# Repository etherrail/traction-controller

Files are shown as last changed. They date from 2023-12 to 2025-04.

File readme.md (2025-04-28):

# EtherRail Traction Controller TC1000PX22+D+EA
The WiFi based controller for locomotives and other rolling stock.
This device is a drop in replacement for any DCC boards.

Main Features
- WiFi enabled
- Plux2 Interface according to [NEM 658](./documentation/nem658.pdf)
- Inertia Sensor for speed control (instead of the common power control)
- Sound up to 96kHz
- 1A motor current (3.6A Peak)
- Track power probe
- Low production cost
- Tip over, stall and push detection

Product Code
- `TC` traction controller
- `1000` 1000mA nominal current
- `PX22` PluX22 plugging interface (NEM 658)
- `+D` debugging version (USB compatible, status LEDs)
- `+CA` external antenna

## To Do
- Test Boards (currently in production)
- Add GPIO pins

## Connectivity
The device connects with WiFi or Bluetooth.
An external antenna should be attached.

## Ineria Sensor
Usually, the trains are controlled by setting a motor power level, not a target speed. The IMU sensor integrates an accelerometer and a gyroscope, which can be used to estimate the actual speed of the train.

No more speed calibrations and motor ramps - the controller can automatically compensate for heavier trains or gradients. Stalling can be detect too, both total stalling and wheel-slip, which can then be counter acted with automatically induced power bursts. The controller can detect being pushed too, for example in a collision case. And even a tip over can be detected.

## Track Power Probe
The traction controller constantly measures the track voltage.
When an outage is detected (which usually happens every couple miliseconds, even with clean tracks), the controller goes into sleep mode to preserve energy on the on board capacitor bank.

This can be used to monitor the tracks quality and schedule maintenance before issues arise.

## Sound
The board contains a 3.2W@4Ohm sound chip.

To be tested.

## Function Outputs
600mA per channel.

Warning: The output are directly connected to the P-Channel mosfets, additional protected may be required for some output devices.

## Expandability
The processor used on this device (ESP32C3) is more than capable for this task.
We could add camera functionality with this chip!
DCC emulation is theoretically possible.

The board currently contains a full USB debugging interface (pads only, but a programmer is included on the ESP).

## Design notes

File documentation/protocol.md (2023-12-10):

# Traction Controller Client Protocol (TCCP)
This document describes the TCP-socket based protocol used to interface with etherrail traction controllers. This protocol may be used by any other Wifi-based traction controller, but modifications should be posed as issues on here to create a common standard.

The traction controller does not store **any** settings. Every setting has to be reapplied on startup.

## Sent by traction controller
Listed are the packages sent by the traction controller.
A orchestrator has to handle all the messages sent by traction controllers.

### `0x00` Keep Alive
The traction controller will send this package every **250ms**. The traction controller should be flagged as dead when no package (not just keep alive) was received for over **1000ms**.

### `0x21 [Quality]` Power Quality
The traction controller may periodically send this package to report the current track quality. We are sending it every 25mm in testing, but this may be decreased and only reported when the quality is poor. 

The quality parameter ranges from 0 (0V track voltage) to 255 (20V track voltage).

## Sent by orchestrator
The orchestrator sends commands to the traction controller. All commands are listed here.

### `0x00` Keep Alive
This package should be sent every **250ms**. The orchestrator has to send any package every **1000ms** or the traction controller will automatically perform an emergency stop. 

### `0x01` Emergency Stop
The traction controller will perform and emergency stop.

### `0x91 [Speed]` Set Speed
The traction controller will apply the speed as a voltage to the motor. 

Speed 0 will stop the motor, while 255 will apply the maximum voltage set by [Maximum Motor Voltage](#0xa1-max-voltage-maximum-motor-voltage).

### `0xa1 [Max Voltage]` Maximum Motor Voltage
This setting prevents motor damage. Any speed operations will automatically be scaled by the maximum voltage. Max voltage parameter ranges from 0 = 0V to 255 = 20V. 

Example: `0xa1 0x7f 0x91 0xff` will apply 10V to the motor, while a following `0x91 0x7f` will apply 5V.

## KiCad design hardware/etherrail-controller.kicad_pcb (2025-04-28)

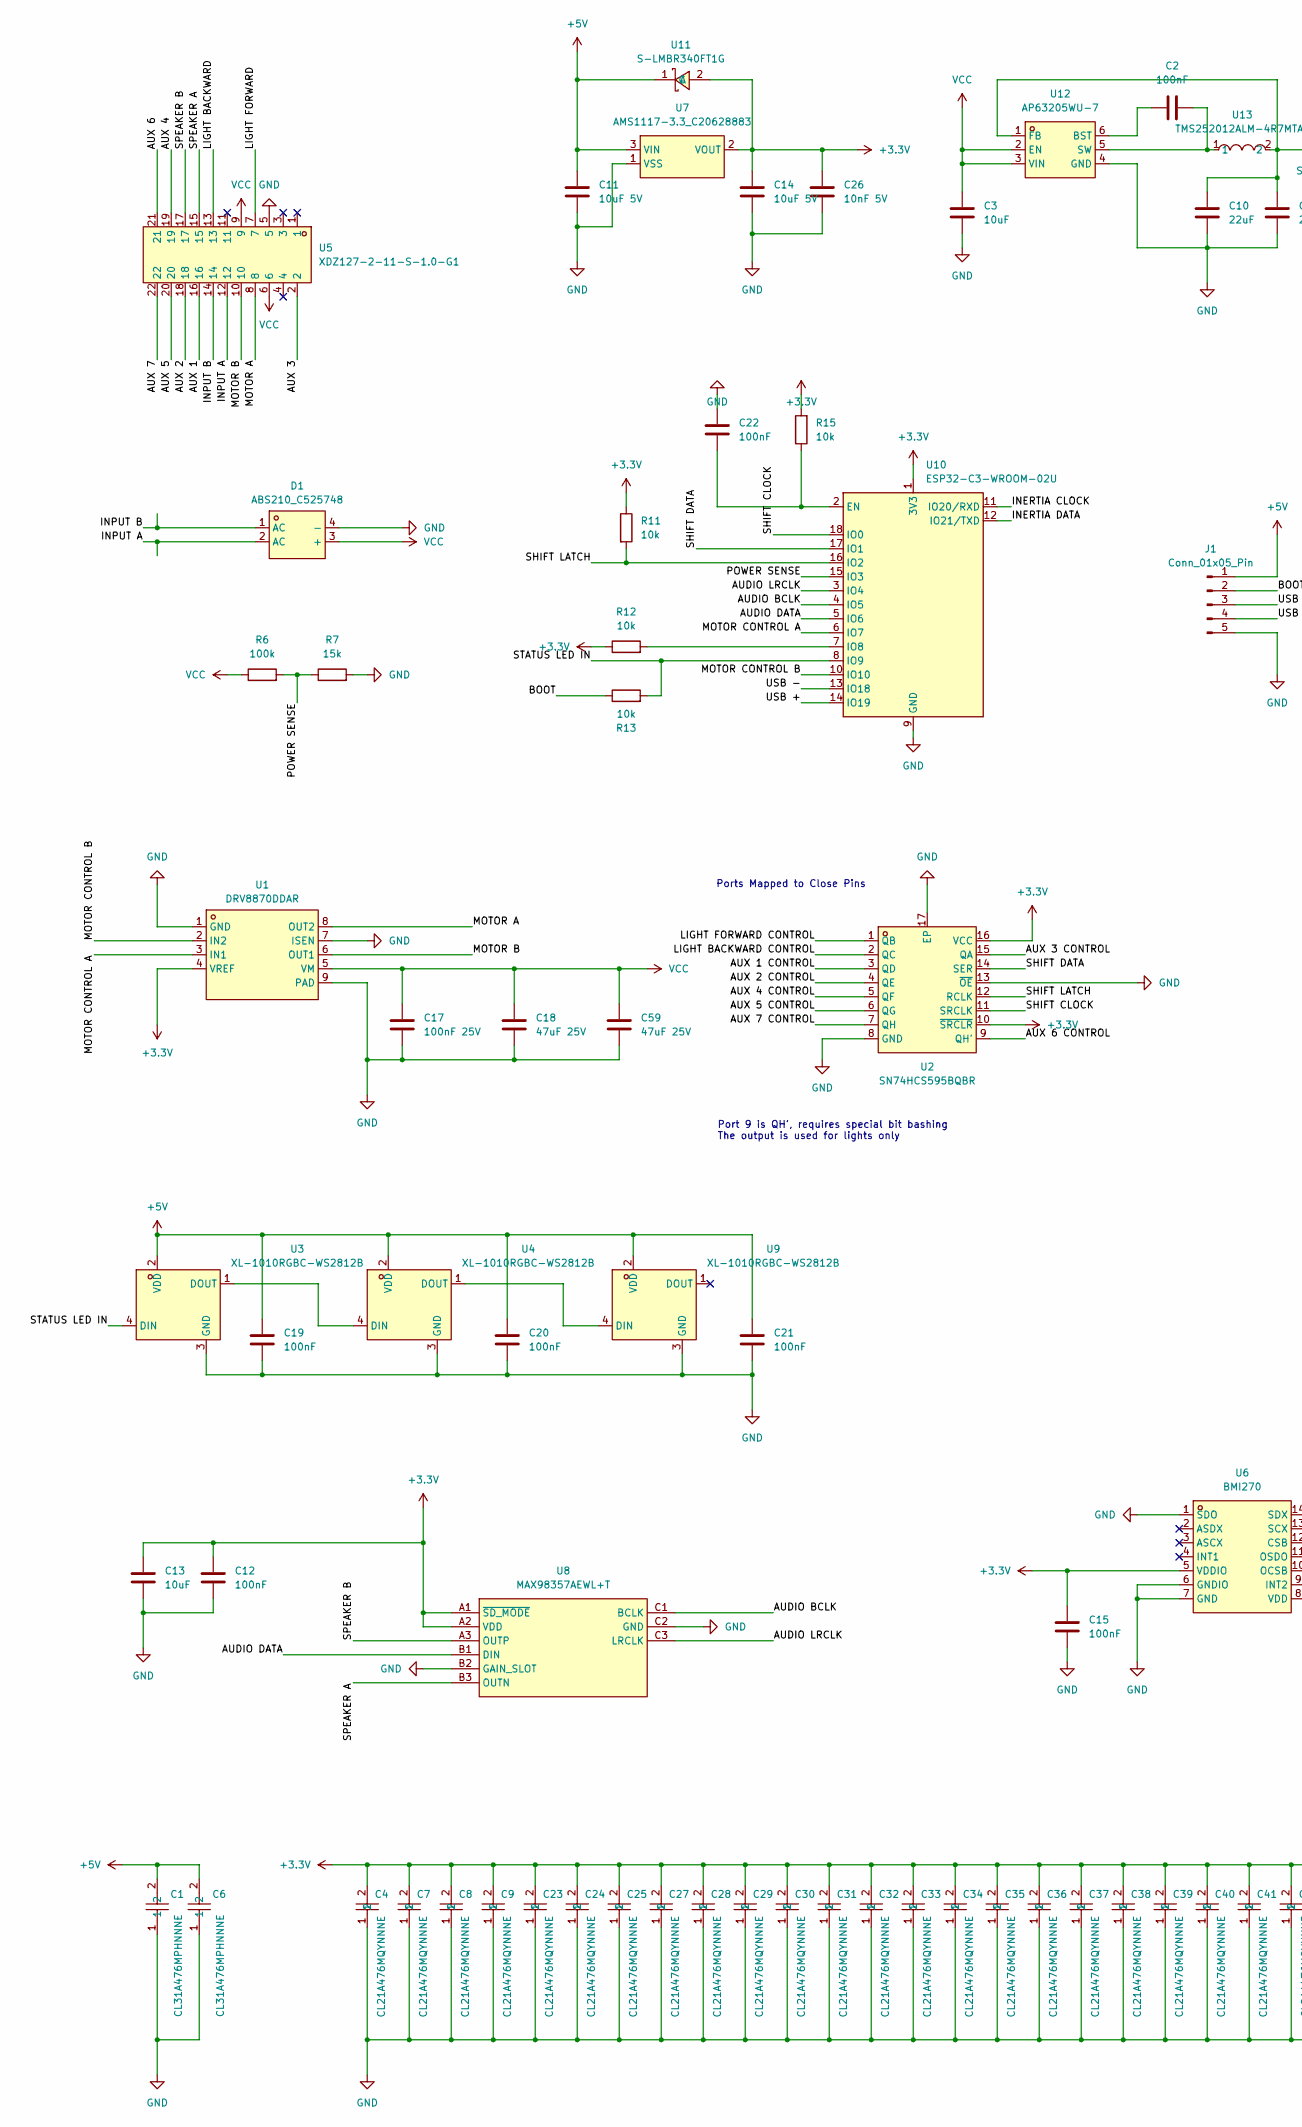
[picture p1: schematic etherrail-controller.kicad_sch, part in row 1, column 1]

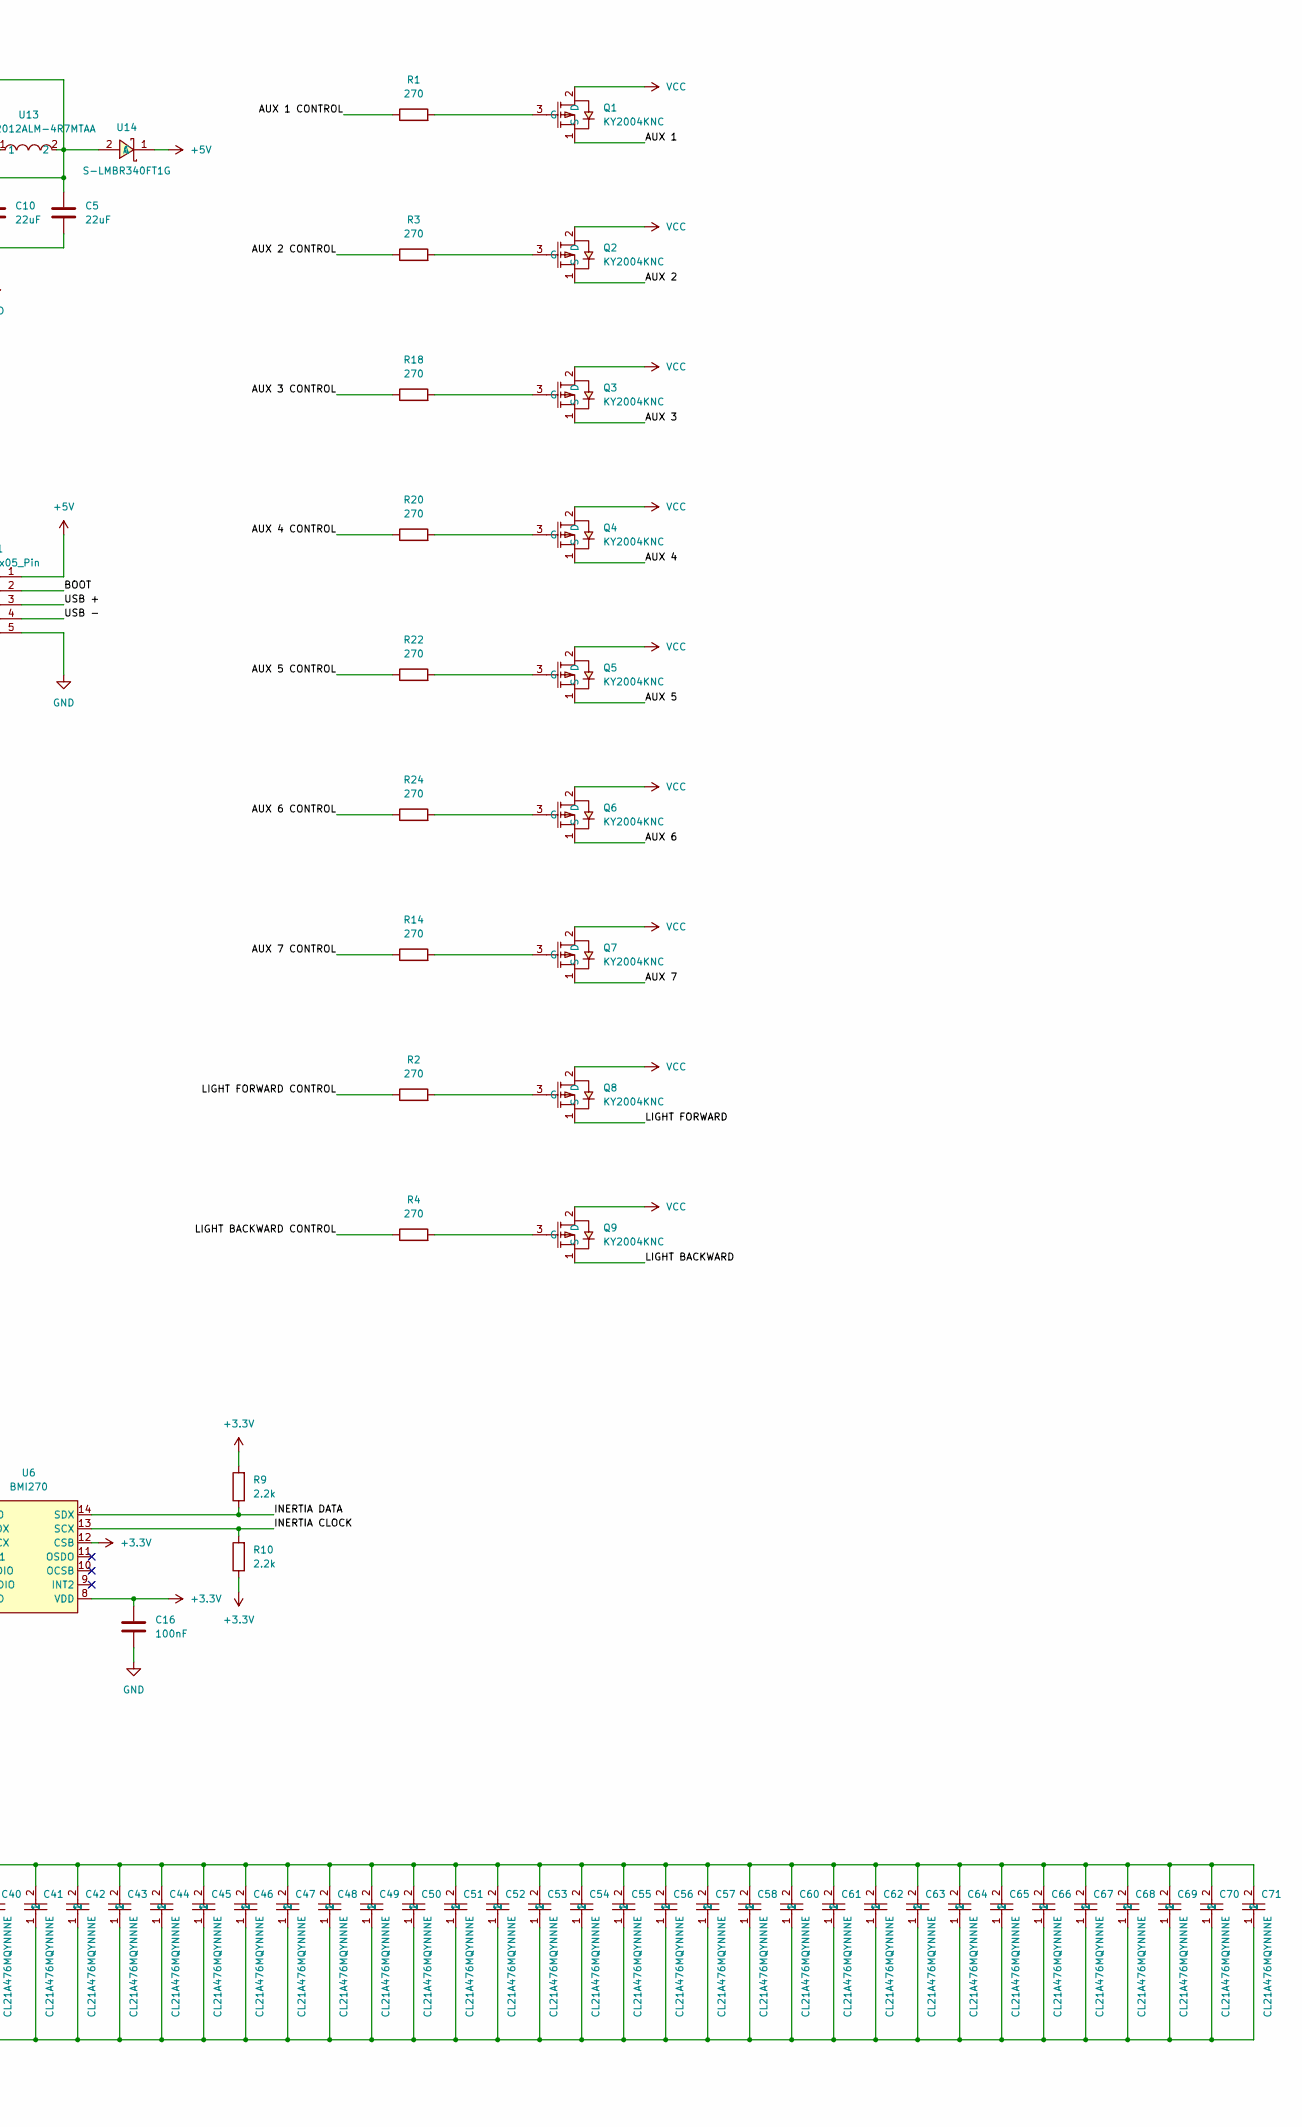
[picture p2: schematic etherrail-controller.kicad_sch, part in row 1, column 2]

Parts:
C1, C6: CL31A476MPHNNNE; C1206; LCSC Part C96123
C2, C22: 100nF; C_0402_1005Metric
C3, C13: 10uF; C_0402_1005Metric
C4, C7, C8, C9, C23, C24, C25, C27, C28, C29, C30, C31, C32, C33, C34, C35, C36, C37, C38, C39, C40, C41, C42, C43, C44, C45, C46, C47, C48, C49, C50, C51, C52, C53, C54, C55, C56, C57, C58, C60, C61, C62, C63, C64, C65, C66, C67, C68, C69, C70, C71: CL21A476MQYNNNE; C0805; LCSC Part C16780
C5, C10: 22uF; C_0402_1005Metric
C11, C14: 10uF 5V; C_0402_1005Metric
C12, C15, C16, C19, C20, C21: 100nF; C_0201_0603Metric
C17: 100nF 25V; C_0402_1005Metric
C18, C59: 47uF 25V; C_1206_3216Metric
C26: 10nF 5V; C_0402_1005Metric
D1: ABS210_C525748; ABS_L5.1-W4.4-P3.35-LS6.4-BL; LCSC Part C525748
J1: Conn_01x05_Pin; DebugPad
Q1, Q2, Q3, Q4, Q5, Q6, Q7, Q8, Q9: KY2004KNC; DFN1006-3L_L1.0-W0.6-BL; LCSC Part C3029285
R1, R2, R4, R24: 270; R_0402_1005Metric
R3, R14, R18, R20, R22: 270; R_0201_0603Metric
R6: 100k; R_0402_1005Metric
R7: 15k; R_0402_1005Metric
R9, R10: 2.2k; R_0201_0603Metric
R11, R13, R15: 10k; R_0402_1005Metric
R12: 10k; R_0201_0603Metric
U1: DRV8870DDAR; HSOP-8_L5.0-W4.0-P1.27-LS6.2-BL-EP; LCSC Part C86590
U2: SN74HCS595BQBR; DQFN-16_L3.5-W2.5-P0.50-BL-EP; LCSC Part C2876392
U3, U4, U9: XL-1010RGBC-WS2812B; LED-SMD_4P-L1.0-W1.0-TL_XL-1010RGBC-WS2812B; LCSC Part C5349953
U5: XDZ127-2-11-S-1.0-G1; HDR-SMD_22P-P1.27-V-M-R2-C11-LS5.5_1; LCSC Part C19268852
U6: BMI270; LGA-14_L3.0-W2.5-P0.50-BR; LCSC Part C2836813
U7: AMS1117-3.3_C20628883; SOT-89-3_L4.5-W2.5-P1.50-LS4.1-BR-1; LCSC Part C20628883
U8: MAX98357AEWL+T; WLP-9_L1.4-W1.3-P0.40-R3-C3-BR; LCSC Part C2682619
U10: ESP32-C3-WROOM-02U
U11, U14: S-LMBR340FT1G; SOD-123FL_L2.7-W1.8-LS3.8-RD; LCSC Part C2972823
U12: AP63205WU-7; TSOT-23-6_L2.9-W1.6-P0.95-LS2.8-BL; LCSC Part C2071056
U13: TMS252012ALM-4R7MTAA; L1008; LCSC Part C5159366

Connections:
+3.3V: C4.2, C7.2, C8.2, C9.2, C12.2, C13.2, C14.2, C15.2, C16.2, C23.2, C24.2, C25.2, C26.2, C27.2, C28.2, C29.2, C30.2, C31.2, C32.2, C33.2, C34.2, C35.2, C36.2, C37.2, C38.2, C39.2, C40.2, C41.2, C42.2, C43.2, C44.2, C45.2, C46.2, C47.2, C48.2, C49.2, C50.2, C51.2, C52.2, C53.2, C54.2, C55.2, C56.2, C57.2, C58.2, C60.2, C61.2, C62.2, C63.2, C64.2, C65.2, C66.2, C67.2, C68.2, C69.2, C70.2, C71.2, R9.2, R10.1, R11.1, R12.1, R15.2, U1.4 (VREF), U2.10 (~SRCLR), U2.16 (VCC), U6.5 (VDDIO), U6.8 (VDD), U6.12 (CSB), U7.2 (VOUT), U8.A1 (~SD_MODE), U8.A2 (VDD), U10.1 (3V3), U11.2 (A)
+5V: C1.2, C6.2, C11.2, C19.2, C20.2, C21.2, J1.1, U3.2 (VDD), U4.2 (VDD), U7.3 (VIN), U9.2 (VDD), U11.1 (C), U14.1 (C)
/AUDIO BCLK: U8.C1 (BCLK), U10.4 (IO5)
/AUDIO DATA: U8.B1 (DIN), U10.5 (IO6)
/AUDIO LRCLK: U8.C3 (LRCLK), U10.3 (IO4)
/AUX 1: Q1.1 (S), U5.16
/AUX 1 CONTROL: R1.1, U2.3 (QD)
/AUX 2: Q2.1 (S), U5.18
/AUX 2 CONTROL: R3.1, U2.4 (QE)
/AUX 3: Q3.1 (S), U5.2
/AUX 3 CONTROL: R18.1, U2.15 (QA)
/AUX 4: Q4.1 (S), U5.19
/AUX 4 CONTROL: R20.1, U2.5 (QF)
/AUX 5: Q5.1 (S), U5.20
/AUX 5 CONTROL: R22.1, U2.6 (QG)
/AUX 6: Q6.1 (S), U5.21
/AUX 6 CONTROL: R24.1, U2.9 (QH')
/AUX 7: Q7.1 (S), U5.22
/AUX 7 CONTROL: R14.1, U2.7 (QH)
/BOOT: J1.2, R13.1
/INERTIA CLOCK: R10.2, U6.13 (SCX), U10.11 (IO20/RXD)
/INERTIA DATA: R9.1, U6.14 (SDX), U10.12 (IO21/TXD)
/INPUT A: D1.2 (AC), U5.12
/INPUT B: D1.1 (AC), U5.14
/LIGHT BACKWARD: Q9.1 (S), U5.13
/LIGHT BACKWARD CONTROL: R4.1, U2.2 (QC)
/LIGHT FORWARD: Q8.1 (S), U5.7
/LIGHT FORWARD CONTROL: R2.1, U2.1 (QB)
/MOTOR A: U1.8 (OUT2), U5.8
/MOTOR B: U1.6 (OUT1), U5.10
/MOTOR CONTROL A: U1.3 (IN1), U10.6 (IO7)
/MOTOR CONTROL B: U1.2 (IN2), U10.10 (IO10)
/POWER SENSE: R6.2, R7.1, U10.15 (IO3)
/SHIFT CLOCK: U2.11 (SRCLK), U10.18 (IO0)
/SHIFT DATA: U2.14 (SER), U10.17 (IO1)
/SHIFT LATCH: R11.2, U2.12 (RCLK), U10.16 (IO2)
/SPEAKER A: U5.15, U8.B3 (OUTN)
/SPEAKER B: U5.17, U8.A3 (OUTP)
/STATUS LED IN: R13.2, U3.4 (DIN), U10.8 (IO9)
/USB +: J1.3, U10.14 (IO19)
/USB -: J1.4, U10.13 (IO18)
GND: C1.1, C3.1, C4.1, C5.1, C6.1, C7.1, C8.1, C9.1, C10.1, C11.1, C12.1, C13.1, C14.1, C15.1, C16.1, C17.1, C18.1, C19.1, C20.1, C21.1, C22.1, C23.1, C24.1, C25.1, C26.1, C27.1, C28.1, C29.1, C30.1, C31.1, C32.1, C33.1, C34.1, C35.1, C36.1, C37.1, C38.1, C39.1, C40.1, C41.1, C42.1, C43.1, C44.1, C45.1, C46.1, C47.1, C48.1, C49.1, C50.1, C51.1, C52.1, C53.1, C54.1, C55.1, C56.1, C57.1, C58.1, C59.1, C60.1, C61.1, C62.1, C63.1, C64.1, C65.1, C66.1, C67.1, C68.1, C69.1, C70.1, C71.1, D1.4 (-), J1.5, R7.2, U1.1 (GND), U1.7 (ISEN), U1.9 (PAD), U2.8 (GND), U2.13 (~OE), U2.17 (EP), U3.3 (GND), U4.3 (GND), U5.5, U6.1 (SDO), U6.6 (GNDIO), U6.7 (GND), U7.1 (VSS), U8.B2 (GAIN_SLOT), U8.C2 (GND), U9.3 (GND), U10.9 (GND), U10.19 (GND), U12.4 (GND)
unnamed: Q1.3 (G), R1.2
unnamed: Q2.3 (G), R3.2
unnamed: Q3.3 (G), R18.2
unnamed: Q4.3 (G), R20.2
unnamed: Q5.3 (G), R22.2
unnamed: Q6.3 (G), R24.2
unnamed: Q7.3 (G), R14.2
unnamed: Q8.3 (G), R2.2
unnamed: Q9.3 (G), R4.2
unnamed: U3.1 (DOUT), U4.4 (DIN)
unnamed: U4.1 (DOUT), U9.4 (DIN)
unnamed: C22.2, R15.1, U10.2 (EN)
unnamed: R12.2, U10.7 (IO8)
unnamed: C2.1, U12.6 (BST)
unnamed: C5.2, C10.2, U12.1 (FB), U13.2, U14.2 (A)
unnamed: C2.2, U12.5 (SW), U13.1
VCC: C3.2, C17.2, C18.2, C59.2, D1.3 (+), Q1.2 (D), Q2.2 (D), Q3.2 (D), Q4.2 (D), Q5.2 (D), Q6.2 (D), Q7.2 (D), Q8.2 (D), Q9.2 (D), R6.1, U1.5 (VM), U5.6, U5.9, U12.2 (EN), U12.3 (VIN)

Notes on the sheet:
Ports Mapped to Close Pins
Port 9 is QH', requires special bit bashing The output is used for lights only

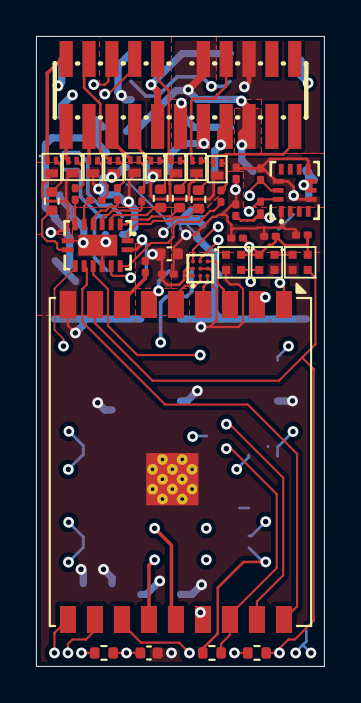
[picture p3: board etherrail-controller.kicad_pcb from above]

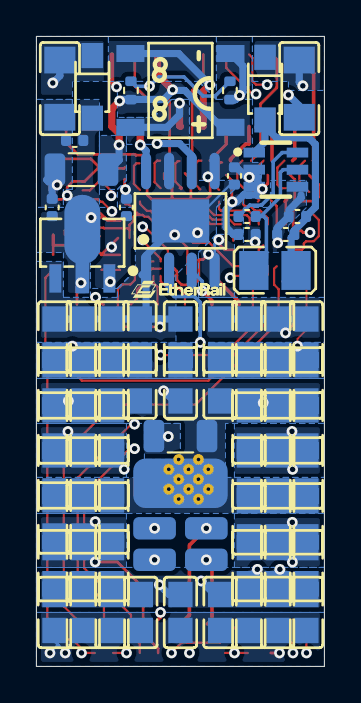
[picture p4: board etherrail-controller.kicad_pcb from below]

Board: 6 copper layers, 16.0 x 35.0 mm, 113 parts (73 on the bottom side), 59 nets.

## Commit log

2023-11-12 Add PCB
    [etherrail-control-1000.kicad_pcb, etherrail-control-1000.kicad_sch]
2023-11-13 Fix 10uF cap footprint
    [etherrail-control-1000.kicad_sch]
2023-11-13 Fix remove kicad symbols
2023-11-13 Add basic readme
    [etherrail-control-1000.kicad_pcb, etherrail-control-1000.kicad_sch]
2023-11-13 Add board area comment
2023-11-13 Add 0402 10uF filter cap to board
    [etherrail-control-1000.kicad_pcb]
2023-11-13 Fix input rectifier ground track power rating
    [etherrail-control-1000.kicad_pcb]
2023-11-13 Fix missing crystal speed property
    [etherrail-control-1000.kicad_sch]
2024-01-13 WIP: Add revised hardware
    [etherrail-control-1000.kicad_pcb, etherrail-control-1000.kicad_sch]
2024-01-13 Fix rename product
    [etherrail-control-1000.kicad_pcb]
2024-01-15 Add EN jumper
    [etherrail-control-1000.kicad_pcb, etherrail-control-1000.kicad_sch]
2024-01-15 Add GPIO2 rotue
    [etherrail-control-1000.kicad_pcb, etherrail-control-1000.kicad_sch]
2024-01-15 Fix use ESP32-C3 with flash (C3-FH4)
    [etherrail-control-1000.kicad_pcb, etherrail-control-1000.kicad_sch]
2024-01-20 Fix connected paths
    [etherrail-control-1000.kicad_pcb]
2025-04-28 Add rewised board with IMU, capacitor bank, PluX22 interface and sound.
    [etherrail-control-1000.kicad_pcb, etherrail-control-1000.kicad_sch, etherrail-controller.kicad_pcb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]
